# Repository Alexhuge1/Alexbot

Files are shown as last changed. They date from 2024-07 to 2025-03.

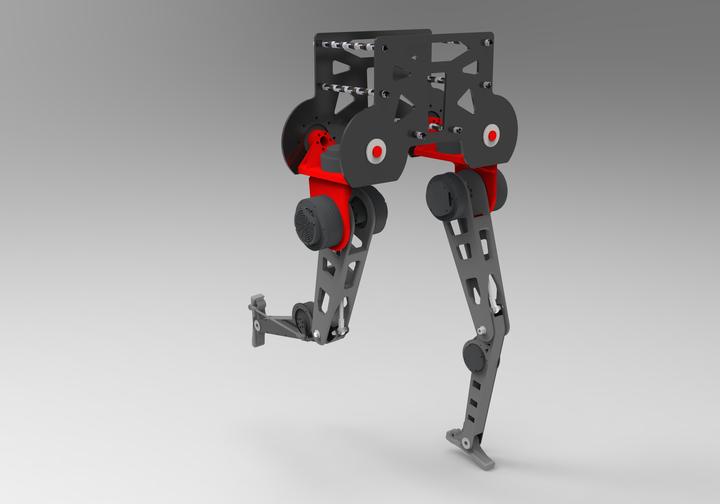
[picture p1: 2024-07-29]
Alexbot.jpeg

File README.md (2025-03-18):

latest version in https://github.com/Alexhuge1/Alexbotmini_hardware
建议直接使用第二代机器人，我们第三代在研发中，用的也是dm电机
## Language

- [English](#english)
- [中文](#中文)

---

### English

AlexBot is an open-source bipedal robots, designed with enhanced performance and a more rational structure. We have developed a complete set of open-source hardware for the robot, including the driving system, which allows it to walk dynamically. While it may not match the performance of commercial robots like the Unitree H1, our design is open-source and cost-effective.

<div style="text-align: center;">
    run
</div>

### Mechanical & Structure

Our robot features a leg with five joints: a 3-DOF hip joint, a 1-DOF knee joint, and a 1-DOF ankle joint. To reduce the overall inertia of the lower leg, we have moved the knee joint motor to the hip area. We use the Daimiao DM-J8009 for the hip joint of the thigh, with a rated torque of 20Nm and a peak torque of 40Nm. Other joints use DM-J8006, and the ankle joint uses DM-J6006. The mechanical design was done in SolidWorks 2021, with topological optimization and structural finite element simulation using Altair Inspire. The thigh parts are CNC machined, with an estimated cost of around 5000 RMB.

<div style="text-align: center;">
    Mechanical Design
</div>

### Hardware & Actuators

The hardware includes an STM32H7B0 core board with a 9-axis gyroscope for outer loop control. The upper computer uses an NVIDIA Jetson Xavier NX, and we are considering whether the TX2 could also be suitable. The entire circuit includes two power distribution boards, a control board with the STM32H7B0VBT6 as the core, and the Jetson Xavier NX as the upper computer. The power supply provides 24V to the motors, with a step-down module to provide 5V and 19V for the control board and Jetson Xavier NX, respectively.

<div style="text-align: center;">
    Hardware Overview
</div>

### Imitation Learning, Full-Body MPC, and WBC

Our gait planning is showing promising results, and the team responsible for the algorithms has successfully made the robot walk. We have adjusted the joint limits in the URDF file according to the electrical control specifications, which can be viewed using the MuJoCo viewer.

<div style="text-align: center;">
    Gait Planning
</div>

### Pricing

The total cost of the robot is estimated to be around 20,000 RMB. We have negotiated a price with Daimiao Motors, and they have agreed to provide the complete set of motors for 10,500 RMB, including a USB-to-CAN module and an H723 development board. The machining cost is estimated to be 6,000 RMB, and adding the Jetson and various bearings and standard parts, the total cost should be around 20,000 RMB.

### Documentation

Our open-source documentation includes中期文档和PPT, which are available for download. For more detailed technical information, please refer to our [Zhihu article](https://zhuanlan.zhihu.com/p/69235601413).

### Community

Our WeChat group has reached its maximum capacity, and we are now using an invitation-only system. Several individuals or teams have already successfully replicated our robot, BOM is updated.

---

### 中文

AlexBot是我们开源双足机器人的下一代产品，设计上注重提升性能和结构合理性。我们为机器人开发了一整套开源硬件，包括驱动系统，使其能够动态行走。虽然它的性能可能远远无法与Unitree H1等商业机器人相媲美，但我们的设计是开源且成本效益高的。

<div style="text-align: center;">
    运行图
</div>

#### 机械与结构

我们的机器人腿部设计有五个关节：3自由度的髋关节、1自由度的膝关节和1自由度的踝关节。为了降低小腿的整体惯量，我们将膝关节电机上移至髋部。我们使用达妙DM-J8009作为大腿的髋关节电机，额定扭矩为20Nm，峰值扭矩为40Nm。其他关节使用DM-J8006，踝关节使用DM-J6006。机械设计是在SolidWorks 2021中完成的，采用了拓扑优化和结构有限元仿真，使用的是Altair Inspire。大腿部分采用CNC加工，预计成本约为5000元人民币。

<div style="text-align: center;">
    机械设计图
</div>

#### 硬件与驱动器

硬件部分主要包括一个集成了九轴陀螺仪的STM32H7B0核心板，用于外环控制。上位机使用了英伟达的Jetson Xavier NX作为主电脑，我们也在考虑是否TX2也能够胜任。整个电路包括两个分电板、一个以STM32H7B0VBT6为核心的控制板和Jetson Xavier NX。电源为电机提供24V电压，并通过降压模块为控制板和Jetson Xavier NX提供5V和19V电压。

<div style="text-align: center;">
    硬件概览
</div>

#### 模仿学习算法、全身MPC和WBC

我们的步态规划已经取得了初步成果，负责算法的团队已经成功让机器人行走。我们根据电控的限位要求调整了URDF文件中的关节限制，可以通过MuJoCo查看器查看。

<div style="text-align: center;">
    步态规划
</div>

#### 价格部分

机器人的整体价格预计在20000元人民币左右。我们已经与达妙电机谈妥价格，他们同意以10500元人民币的价格提供整套电机，并附送USB转CAN模块和H723开发板。加工费用预计为6000元人民币，加上Jetson和各种轴承及标准件，总成本应该在20000元人民币左右。

我们的开源文档包括中期文档和PPT，可供下载。有关更详细的技术信息，请参阅我们的[知乎文章](https://zhuanlan.zhihu.com/p/69235601413)。

#### 社区

我们的微信群已满200人，现在采用邀请制度。已有数人成功复制了我们的机器人，BOM已更新。

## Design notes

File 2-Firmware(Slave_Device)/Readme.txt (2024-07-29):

How to use the code
leg02包含了USART01与上位机(Jetson)通讯、CAN1接左腿五电机级联、CAN2接右腿五电机级联、SPI通讯接受BMI088数据
包含了时钟，定时器等底层设计，同时进行了一些些简单的封装，方便基于函数开发，简单介绍一下程序架构：
1.在dm_driver.c中,其中电机使用MIT协议进行力控，使用void mit_ctrl(FDCAN_HandleTypeDef* hcan, uint16_t motor_id, float pos, float vel,float kp, float kd, float torq)来控制。
2.在Frame_function.c，写了上下位机通信的部分，包含了下位机的接收和发送，其中规定了帧的格式，如果传参变量发生修改请修改此函数。
3.在BMI088driver.c中，写了六轴加速度计的部分，包含了姿态解算得到姿态的欧拉角和加速度，同时还写了函数包含了使用四阶龙格库塔法来解算从欧拉角变到四元数。
----------------------------------------------------------------------------------------------
leg02 contains a USART01 and the host computer (Jetson) communication, CAN1 to the left leg of the five motor cascade, CAN2 to the right leg of the five motor cascade, SPI communication to accept BMI088 data.
Contains a clock, timer and other underlying design, while some of the simple package, to facilitate the development of function-based, simple introduction to the program structure:
1. in dm_driver.c, where the motor using the MIT protocol for force control, using void
 mit_ctrl(FDCAN_HandleTypeDef* hcan, uint16_t motor_id, float pos, float
 vel,float kp, float kd, float torq) to control.
2. In Frame_function.c, write the upper and lower computer communication part, including the lower computer to receive and send, which specifies the format of the frame, if the pass parameter variable is changed, please modify this function.
3. In BMI088driver.c, wrote the part of the six-axis accelerometer, which contains the attitude solving to get the Euler angle and acceleration of the attitude, and also wrote the function which contains the solving to change from Euler angle to quaternion by using the fourth-order Lunger Kuta method.

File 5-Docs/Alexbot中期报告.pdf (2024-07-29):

## 哈尔滨工业大学

## 大学生创新创业训练计划项目

## 中期检查报告

### 项 目 名 称：双足人形机器人 AlexBot

### 执 行 时 间： 2023 年 9 月至 2024 年 9 月

# 负 责 人：黄一 Alexhuge

### 学院及专业：未来技术学院

## 1、项目简介

现拟打算设计一套以伺服电机为驱动器的十自由度的双足机器人下肢 AlexBot，以研究双

足机器人运动规划与控制，首先对于机器人的结构以及控制系统进行设计以及拓扑优化；其 次，进行以髋部坐标系为基坐标系的正运动学及逆运动学分析，并计算了机器人的实时质心 位置以及机器人的质心相对于足端的雅可比矩阵；随后，说明了基于质心期望力的二维线性 倒立摆理论，分别对单足支撑阶段以及双足支撑阶段的支撑脚与摆动脚进行规划，再将二维 的情况推展到三维；之后，将线性倒立摆的行走数据当作参考在虚拟环境中对机器人进行强 化学习训练，其中包括神经网络的结构的设计，强化学习算法超参数的设置，奖励函数、训 练终止条件的设置以及将仿真迁移到现实机器人中需要进行的动态随机化策略；最后，为了 验证方法的可行性，分别在仿真以及现实中实验。

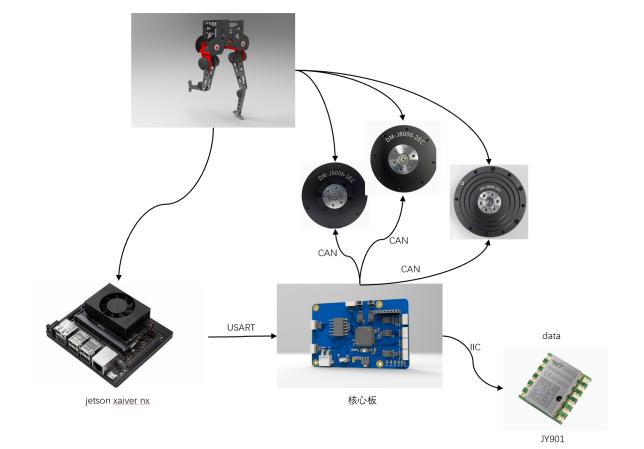
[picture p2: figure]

图 1-1 AlexBot 双足机器人设计仿真图 | 图 1-2 双足机器人架构图

## 2、立项背景

## 2.1 研究背景

在我国社会结构和经济发展的新阶段，人口老龄化问题已成为一个不容忽视的社会现象。 根据最新的统计数据，65 岁及以上的老年人口数量已经超过 1.8 亿，占总人口的比例达到 12.6%，并且这一比例预计将在未来持续增长。这一趋势的出现，对我国的劳动力市场产生了

显著影响。随着劳动力人口的减少，劳动力成本不断上升，这不仅对传统的经济发展模式提 出了新的挑战，也对现有的社会保障体系带来了前所未有的压力。 在应对人口老龄化的挑战中，机器人产业的发展显示出了巨大的潜力和重要性。通过引 入机器人技术，不仅可以有效缓解劳动力短缺的问题，还能显著提高生产效率和质量，从而 推动经济的持续健康发展。

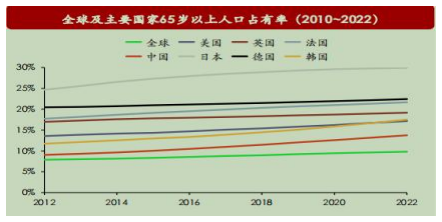
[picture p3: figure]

图 2-1 全球及主要国家 65 岁以上人口占有率

## 2.2 研究目的及意义

随着科技的不断进步，人们对机器人技术的需求和期待也在不断提高。在这一背景下， 足式机器人，尤其是双足机器人的研究和开发成为了机器人领域的热点之一。双足机器人相 较于其他类型的机器人，具有一系列独特的优势和潜力：它们不仅能够提高生产效率，保障 人员安全，还能够在服务领域发挥重要作用，推动人机交互和人机协同技术的发展。

图 2-2 人形机器人应用于人类日常生活

## 2.3 研究现状

从上个世纪中叶开始，双足机器人的研究逐渐成为全球科技领域的热点，研究者们从对 人类和各种动物的步行理论研究开始，随着科学技术领域的飞速发展，双足机器人的行走又 融合了运动控制、人工智能等方式，双足机器人的行走理论被逐渐完善。美国和日本在这一 领域的发展尤为突出，它们的研究成果不仅推动了机器人技术的进步，也引领了全球的研究 趋势。
美国波士顿动力公司的 Atlas 机器人和日本本田公司的 ASIMO 机器人就是近十年来在学 术界引起广泛关注的两大“网红”机器人。这些机器人不仅在技术上取得了飞速的发展，而且

在运动规划和稳定性控制方面也取得了显著的成就。半个世纪以来，这两个国家涌现出了许 多震惊学术界的先进机器人，如本田的 ASIMO 和波士顿动力的 Atlas，它们不仅在技术上达

到了新的高度，而且在实际应用中也展现出了巨大的潜力。

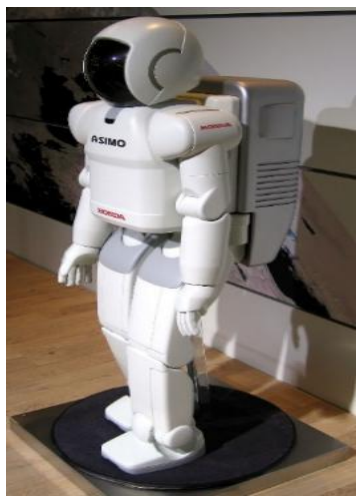
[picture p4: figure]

（a）ASIMO 机器人 | （b）ATLAS 机器人
图 2-3 美国和日本公司研发的部分人形机器人
特斯拉公司的人形机器人 Tesla Bot 在经历了多版本迭代之后，其研究进展远超预期。从

步态行走技术来看，Tesla Bot 从 2022 年完成第一次步态行走到 2023 年已经能够实现在工厂 内稳步行走；从功能来看，Tesla Bot 从第一版仅具备抓取、搬运、上下料功能到具备双手处 理复杂任务的能力，同时 Tesla Bot 关节电机转矩控制的精度已经可以达到在运动过程中不打 碎鸡蛋的水平。与此同时，Tesla Bot 与特斯拉车辆共享核心自研的感知技术（FSD Computer

## 和 DOJO Training），并且其搭载的 Autopilot Camera 所具备的强大的视觉处理能力使得 Tesla

Bot 在人形机器人研究领域处于领先地位。

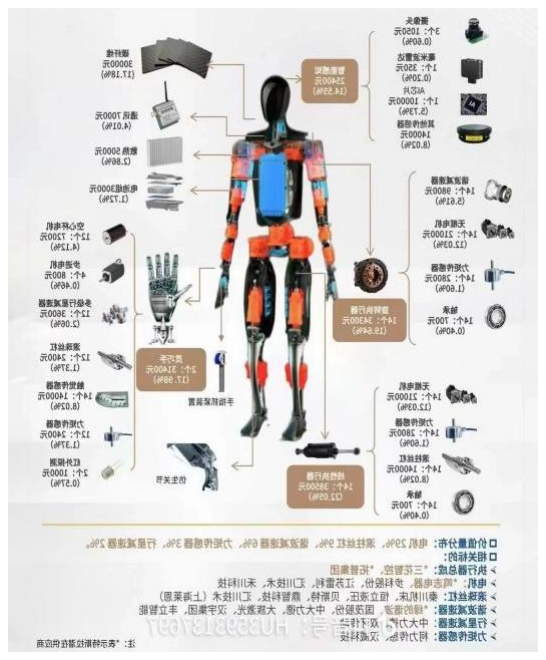
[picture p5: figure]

（a）特斯拉人形机器人 Optimus （b）Optimus 结构示意图

## 图 2-4 特斯拉公司研发的 Tesla Bot

中国在人形机器人产业的发展过程中，经历了从追赶到领先的转变，并逐步超越了早期 投入此领域的日本、美国和韩国。其中创业企业典型代表包括优必选科技、追觅科技、智元、 宇树、傅利叶智能等；科技企业典型代表则为小米、科大讯飞；高校领域则以哈尔滨工业大 学研制的 GoRoBoT 机器人、北京理工大学研制的 BHR 系列双足机器人、清华大学研制的

## Stepper-2D 机器人为代表。

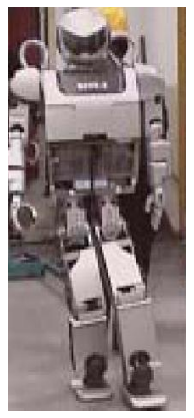
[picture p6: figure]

（a）宇树 H1 机器人（b）傅里叶 GR-1 机器人（c）BHR-2 机器人（d）优必选 Walker 机器人

图 2-5 国内部分双足人形机器人

## 2.4 研究趋势

随着人形机器人产业奇点将至，市场将会呈现出更加明显的马太效应。在未来很长一段 时间内，人形机器人的领域将围绕人类步态与行为的高度模仿、环境感知与交互能力的提升、 轻量化和能效优化等一系列方向进一步深化发展。未来随着技术的不断成熟和创新，人形机 器人尤其是双足机器人有望在更多领域展现其独特的价值和潜力。

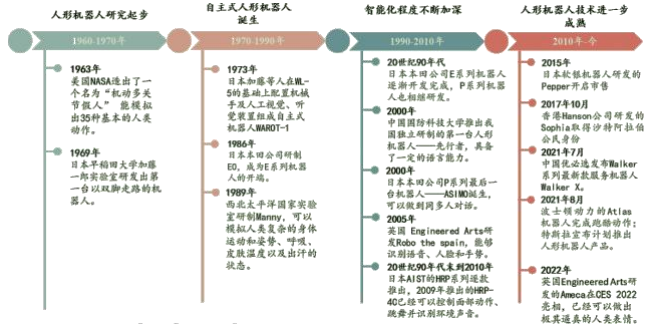
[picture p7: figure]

图 2-6 人形机器人发展历程及未来发展趋势

## 3、项目方案

本项目我们对双足机器人的行走进行研究，通过研究基于质心期望力的二维线性倒立摆 拓展到三维线性倒立摆，并通过强化学习算法得到神经网络控制器，使得双足机器人可以执 行行走任务，主要研究内容如下：
(1) 本项目想设计一套大型伺服双足机器人以供算法研究使用，同时严格控制成本并且编

写教程开源全结构、硬件、算法，提供一套双足的完整的解决方案，产生一定的影响力。
(2) 研究基于二维线性倒立摆的步态规划器，通过线性倒立摆的动力学性质进行规划，分

别对单足支撑期和双足支撑期进行规划，应用足底到质心的雅可比矩阵，将动力学简化模型 应用到复杂机器人上，通过反馈重新分配腿部力矩，使得双足机器人的能量足以越过势能高 点，形成稳态行走的步态，而后再将二维线性倒立摆拓展到三维线性倒立摆算法。
(3) 应用基于质心期望力的线性倒立摆所得到的规划步态形成参考轨迹，使用强化学习算

法，在虚拟环境中迭代训练，运用动态随机化策略，提高网络的适应度，以便将仿真中训练 的网络迁移到现实环境中。
(4) 将网络模型迁移到现实机器人身上，进行 Sim to Real 的行走实验，积累经验，提升机

器人的鲁棒性。

## 4、项目实施的进展情况及初步取得的成果

## 4.0 整体架构

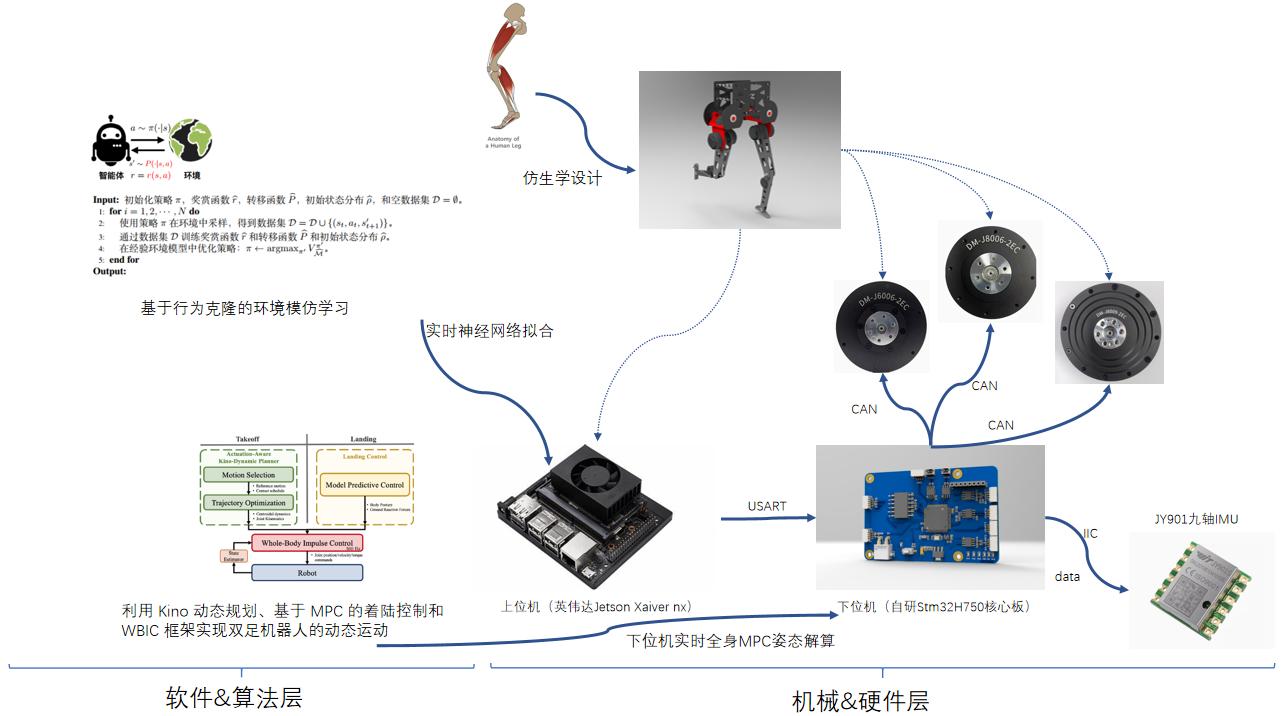
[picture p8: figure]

图 4-1 双足机器人架构图

本项目期望设计一套低成本，全开源，低入门门槛，完整系统的双足下肢机器人（之后 会设计上肢），方便形成双足开源生态，增加影响力和为更多工程师提供帮助。（类比 MIT 的 Cheetah 四足机器人）

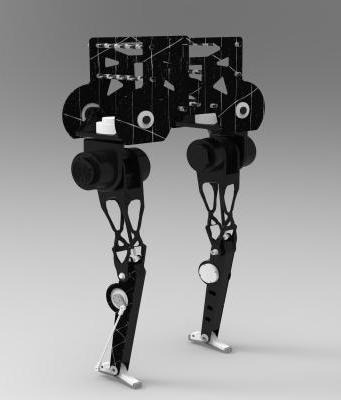
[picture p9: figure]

## 图 4-2(a) MIT Cheetah 四足机器人 图 4-2(b) HIT Alexbot 双足机器人

本项目涉及两套双足机器人结构，一套为研究三维线性倒立摆所需要的十自由度桌面级 机器人，其各个执行器都是在机器人矢状面内出力，配置以人类的下肢关节配置为参考，使 得机器人得以在三维平面内行走。另一套为大型研究步态以及迭代优化双足架构的大型双足 机器人。

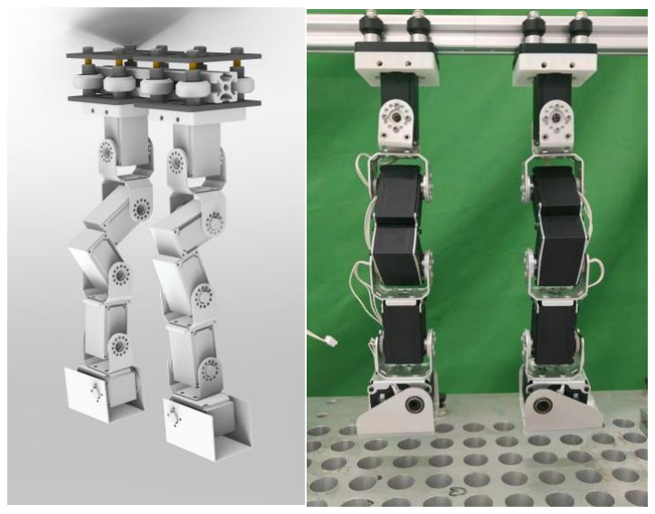
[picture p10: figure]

图 4-3(a) 研究性桌面级双足机器人 | 图 4-3(b) AlexBot 双足机器人下肢

我们先对两套双足机器人结构进行设计，搭建控制系统，此外为后续进行步态规划打下 基础，对两套机器人分别进行正运动以及逆运动学分析，使得给定足端位姿可以求解各关节 角度，给定各关节角度可以求解足端位姿。同时，通过给定关节角度以及髋部位姿，得出机 器人实时的质心位置，求解足端到机器人质心的雅可比矩阵。

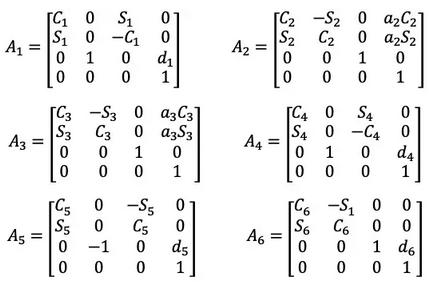
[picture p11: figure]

图 4-4(a) D-H 法正解双足姿态 | 图 4-4(b) D-H 法逆解双足姿态

同时应用对于机器人的运动学计算结合线性倒立摆算法对支撑腿、摆动腿以及双足支撑 阶段进行规划和控制，同时在仿真物理环境 Mujoco 中进行稳定行走，生成二进制数据，通过 agent 与环境的自主迭代互动，向着累计回报最高的方向进化，为了提高效率，同时为了避免

强化学习学习的步态与人类行走步态相差过大，采用基于参考轨迹的强化学习方法，我们利 用近端策略优化的强化学习算法训练神经网络控制器，在基于质心期望力的线性倒立摆的运 动规划器所形成的参考轨迹的基础上进行学习训练，对于算法的流程、状态及动作空间以及 奖励函数进行了设计，引入了动态随机化策略使得网络更容易迁移到现实机器人之中，进行 强化学习步行控制器的设计。

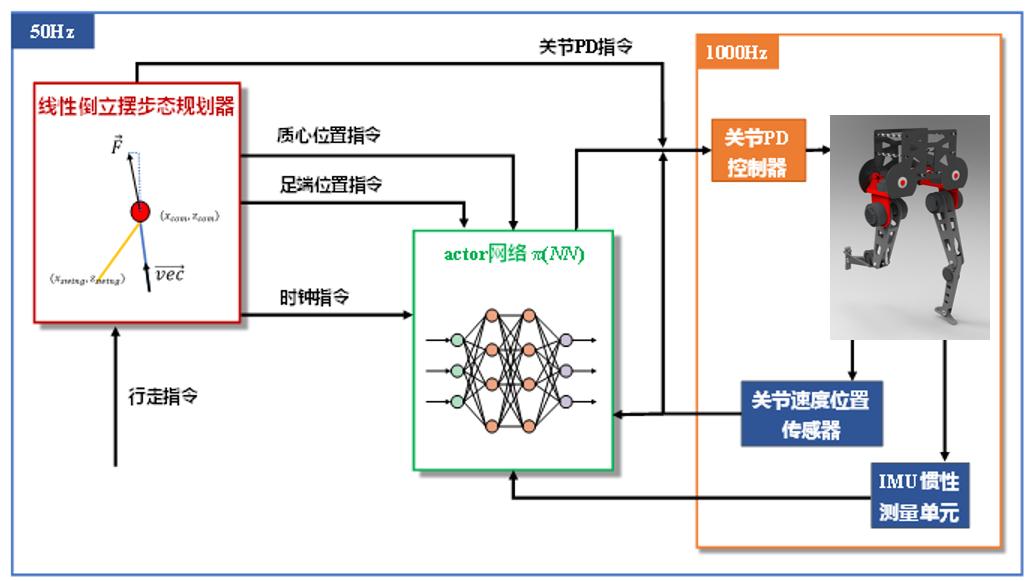
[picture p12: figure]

图 4-5 AlexBot 双足机器人基于倒立摆规划器的神经网络框图

为了验证强化学习的可行性，将从仿真和实物两个层面来进行算法验证。首先在仿真实 验中分别进行机器人的行走实验，由于发现通过强化学习所得到的网络具有一定的鲁棒性， 故额外进行了抗干扰力实验，并进行抗干扰训练提升机器人的抗干扰能力。同时将进行最为 困难的 Sim To Real 迁移实验，实现双足机器人的行走和实现更多动作。

## 4.1 机械部分

4.1.0 机械总论

本项目目标是研制一款双足机器人，具有轻量化的结构以及优秀的性能和合理分配的惯 量以及合适的运动性能。基于轻量化的考虑，本项目首先分析人体腿部结构以及肌肉分布和 腿部惯量，使用一体闭环私服关节电机以及有限元分析 Altair Inspire 分别代表人体的肌肉以

及骨骼，使用最小体积质量比目标对机械腿的框架结构进行优化设计，并将拓扑优化结果导 入到 SolidWorks 软件中，在考虑加工条件的前提下对零件进行修形，得到了满足强度要求且 轻量化的机械腿的结构件。同时，机器人使用轻量化的结构件加工而成，如 3K 碳管，3K 碳 纤维板，铝 6061 等材料，既兼顾材料重量也兼顾材料强度。
AlexBot 双足机器人包含单腿 5 自由度，其中包含三个髋关节自由度、一个膝关节自由度、

一个踝关节自由度。其中为了整体惯量考虑，我们整体上移膝关节自由度并使用板簧结构传 动到膝盖部分，对于踝关节自由度亦如此。通过惯量的计算以及参数测量，我们最终选定三 款一体闭环驱动电机，分别为 DM-J8009、DM-J6006、DM-J8006。具有双编码器，输出轴单

圈绝对位置，不惧掉电输出轴绝对位置丢失。同时电机和驱动器一体化设计，结构紧凑，集 成度高。支持上位机可视化调试，支持固件升级。可通过 CAN 总线反馈电机速度、位置、

转矩、电机温度等信息。位置模式下支持梯形加减速。对于安全方面，具有双温度保护功能， 保证电机稳定运行。

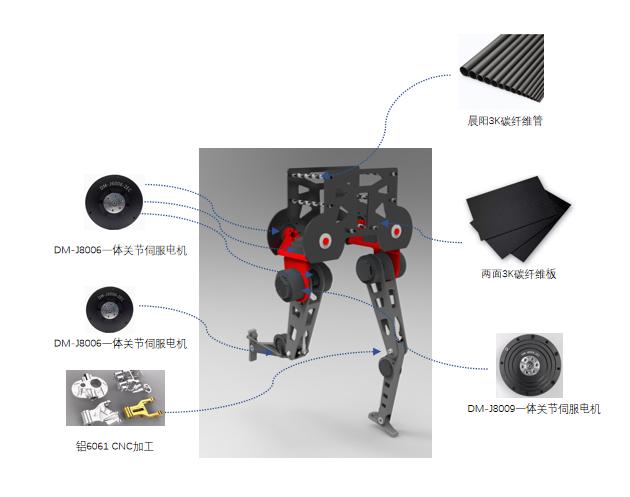
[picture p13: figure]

图 4-6 AlexBot 双足机器人机械结构以及关节自由度分配与限制角度

4.1.1 设计需求分析——腿部结构设计分析

在植物和生物的世界里，生物系统的基本结构往往是向着最优能源消耗的方向进化的， 相比较于现有的机械结构而言，生物结构的重量更轻、寿命更长，并且具有一定的柔性。自 然界生物进化的一个特点是“用进废退”，在需要承受较大载荷的地方会优先进化，在承受较

小载荷的地方，则会发生退化。如长颈鹿的祖先的脖子并没有现在这么长，但是由于气候问 题，较矮的灌木不复存在，为了吃到更高的乔木上的枝叶，长颈鹿的脖子渐渐往长的方向进 化。人类作为灵长类动物，双足步行已有数百万年的历史，因此在机械腿设计中，可以参照 人体运动学和构造来设计机械腿。
人体的腿部结构主要存在 6 个自由度，分别是髋关节的屈伸/伸展（俯仰、pitch）、内旋/ 外旋（偏航、yaw）、外摆/内收（翻滚、roll）三个自由度，膝关节的屈伸/伸展自由度，踝关 节的屈伸/伸展、外摆/内收两个自由度。在本文的设计的柔顺机械腿中，主要研究的自由度为 髋关节和膝关节的屈伸/伸展自由度，这是因为这两个自由度在人体运动中承受了最大的载荷，

直接为人在行走、跳跃、奔跑等过程中重心的位移提供动力。 人体腿部整体外形曲线呈上粗下细的倒三角，如图 4-7 所示，这是因为人在运动过程中腿

部存在支撑相和摆动相这两个状态，倒三角的结构有利于减小腿的转动惯量，提高腿在摆动 相过程中的动态性能。在机械腿设计中，应该参照人体腿部结构，设计符合人体动力学的“上 重下轻”的机械腿。此外，应该尽可能减少机械腿结构的重量，小腿的质量要小于大腿，机械

腿结构重量的降低使得机械腿可以选择更小、更轻的驱动器，减少机械腿质量的同时可以调 高其动力学性能。人体膝关节处有复杂的半月板-韧带结构，如图 4-7 所示，其中，半月板负

责行走、跳跃、奔跑等过程中对外部冲击的缓冲以及膝关节运动的润滑，韧带负责连接肌肉 与骨骼，提供动力。做过半月板切除手术的运动员膝盖往往容易再次受伤，其原因就是在切 除了半月板之后，运动员股骨和胫骨连接初缺少缓冲和润滑，在进行跑跳等动作时膝盖会受

关节 | 自由度 | 角度 (rad)

髋关节

| 横滚 | -0.345~1.222
| 俯仰 | -1.222~1.222
髋关节 | 横滚 | -1.047~1.047
膝关节 | 俯仰 | 0~1.571
踝关节 | 俯仰 | -1.047~1.047

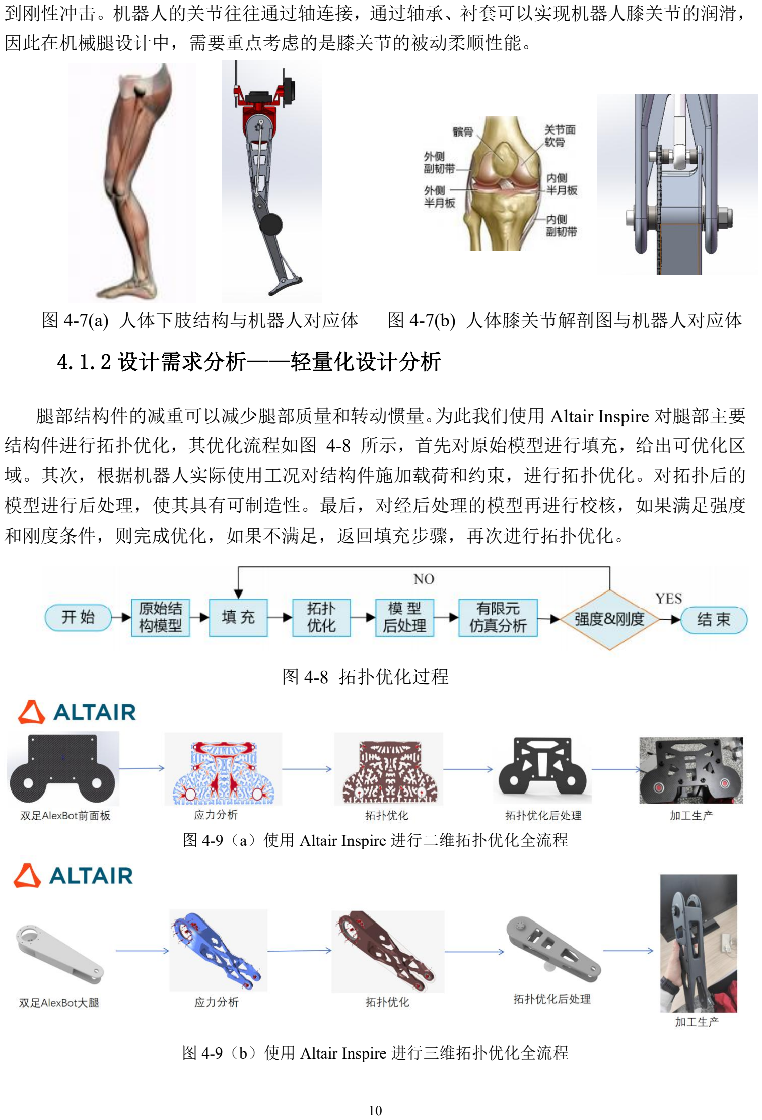
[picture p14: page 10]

到刚性冲击。机器人的关节往往通过轴连接，通过轴承、衬套可以实现机器人膝关节的润滑， 因此在机械腿设计中，需要重点考虑的是膝关节的被动柔顺性能。

图 4-7(a) 人体下肢结构与机器人对应体 图 4-7(b) 人体膝关节解剖图与机器人对应体

4.1.2 设计需求分析——轻量化设计分析

腿部结构件的减重可以减少腿部质量和转动惯量。为此我们使用 Altair Inspire 对腿部主要 结构件进行拓扑优化，其优化流程如图 4-8 所示，首先对原始模型进行填充，给出可优化区

域。其次，根据机器人实际使用工况对结构件施加载荷和约束，进行拓扑优化。对拓扑后的 模型进行后处理，使其具有可制造性。最后，对经后处理的模型再进行校核，如果满足强度 和刚度条件，则完成优化，如果不满足，返回填充步骤，再次进行拓扑优化。

图 4-8 拓扑优化过程

图 4-9（a）使用 Altair Inspire 进行二维拓扑优化全流程

图 4-9（b）使用 Altair Inspire 进行三维拓扑优化全流程

以双足前面板为例，AlexBot 采用前后双碳板通过碳管固定，通过在 Altair Inspire 添加载荷与 固定点实现最小化质量与最大应力比进行 2 维拓扑优化，如图 4-9（a）所示。3 维拓扑优化

同理。

4.1.3 运动周期分析

在机器人行走过程中，可以将一只脚着地到下一次着地这一段时间划分为一个运动周期。 在本文的设计中，不考虑脚掌的设计，仅仅将其看成一个支点，因此可以将行走步态下机械 腿的运动周期划分支撑相和摆动相两个状态。在行走过程中，机械腿需要为整个机器人质心 的运动提供能量支持，在摆动腿落地瞬间，摆动腿切换为支撑腿，依靠机器人自身行走的惯 性和膝关节的伸展 将质心从谷点推动到峰点，随后利用重力和膝关节的弯曲将质心从峰点降 回至谷点，完成支撑相周期，期间髋关节的屈伸/伸展自由度需要配合膝关节的角度实时调整

上半身的质心位置，防止机器人出现倾翻的状况；机器人双腿在摆动相和支撑相中相互切换， 当其中一只腿处于支撑相时另一只腿则处于摆动相，准备下一次与地面接触。具体的步行中 状态变化图如图 4-8 所示。从图中可以看出机器人在运动过程中，机械腿在摆动相和支撑相

的切换瞬间，该腿与地面发生冲击，机器人垂直方向的能量瞬间被释放，在膝关节处的缓冲 就显得尤为重要。虽然本文的线性/弹簧倒立摆步态已经考虑了落地时的冲击，但是在实际工

作过程中，由于控制器与作动器的延迟，冲击依然存在，因此机械腿设计时需要考虑其被动 柔顺性。此外，根据倒立摆模型的建模特性（机器人被看作质心和无重量的腿），在设计时， 机械腿的重量需要尽可能轻，以保证机械腿的动态性能。从运动周期可以看出，机器人机械 腿设计需要重点考虑柔顺性和轻量化，这也与前文的分析不谋而合。我们使用斯坦福大学的 软件 OpenSim 实现人形结构的奔跑对应的肌肉与骨骼运动分析。

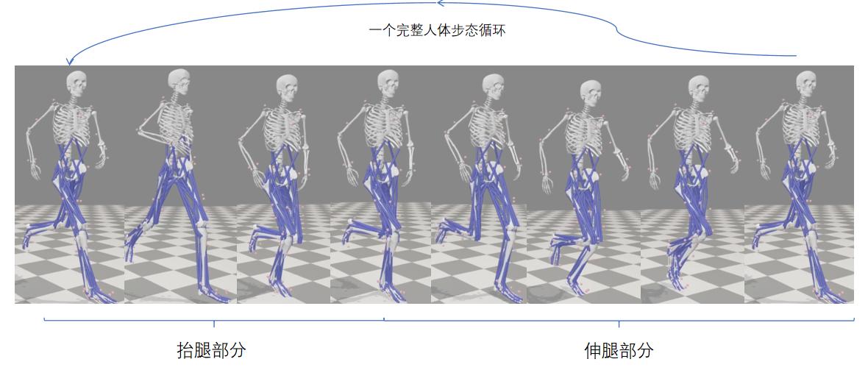
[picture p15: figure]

图 4-8 OpenSim 仿真人体一个完整的跑步姿态

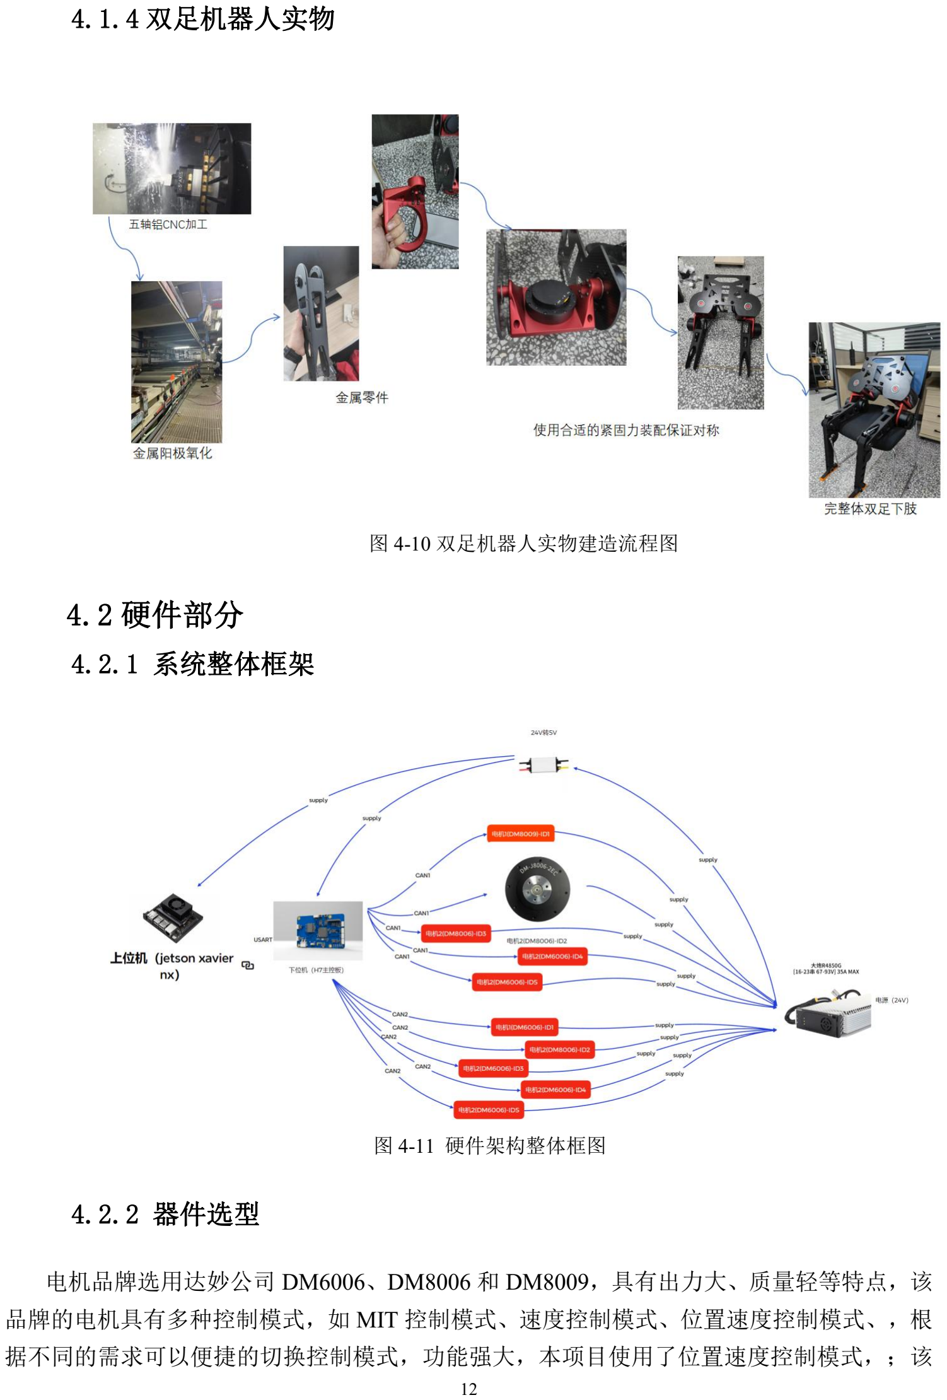
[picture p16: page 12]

4.1.4 双足机器人实物

图 4-10 双足机器人实物建造流程图

## 4.2 硬件部分

4.2.1 系统整体框架

图 4-11 硬件架构整体框图

4.2.2 器件选型

电机品牌选用达妙公司 DM6006、DM8006 和 DM8009，具有出力大、质量轻等特点，该 品牌的电机具有多种控制模式，如 MIT 控制模式、速度控制模式、位置速度控制模式、，根

据不同的需求可以便捷的切换控制模式，功能强大，本项目使用了位置速度控制模式，；该

品牌电机都配备了绝对值编码器，同时响应速度快，满足整个系统对于快速性的要求。 其中三种电机 DM6006 的额定电压为 24V 但支持 48V 输入，额定电流为 4A，额定的扭 矩为 4NM。DM8006 电机的额定电压为 24V 可支持 48V 输入，额定电流为 6.5A，额定的扭 矩为 8NM。DM8009 电机额定电压为 48V，可支持 24V 输入，额定电流为 20A.。考虑到整个 功率以及供电的需求，我们这里统一采用 24V 对三种电机供电，根据不同关节所需的扭矩的

不同，我们分别选取不同的电机。

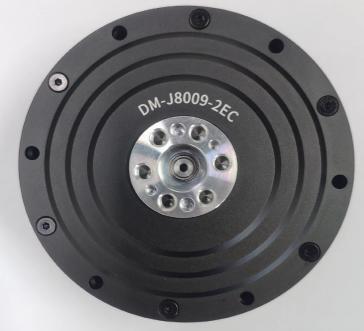
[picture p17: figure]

图 4-12(a) DM-J6006 | 图 4-12(b) DM-J8006 | 图 4-12(c) DM-J8009

IMU 惯性测量单元选用维特智能公司的 WT-901C 型号，其具有精度高，速度快，误差小 等优点，具有六轴和九轴的算法，可以根据需求选取模式，加速度计分辨率为 0.0005

## g/LSB,RMS 噪声在 0.75 到 1 mg-LSB 之间；陀螺仪分辨率为,RMS 噪声在 0.0028 到之间；俯

仰角及横滚角的分辨率为 0.0055°，其倾角精度为 0.2°，可以满足双足机器人使用的反馈精

度。
在电源选取上，我们一共所需四个 DM6006 电机，四个 8006 电机以及两个 DM8009 电机， 根据他们的额定电压和额定电流，这里我们假设他们的输入电压都为 24V，我们可得到总的 功率为 1968W 的功率。所以我们这里选取了输出功率为 2KW 的 DC 直流源作为我们的供电

电源。

图 4-13(a) JY901 九轴传感器 | 图 4-13(b) DC 直流源

4.2.3 硬件设计

整体电路所包含的电路板总共如下，包含两个分电板以及一个 STM32H7B0VBT6 为核心

## 的控制板和上位机 jetson Xavier nx。由电源供电 24V 给到 4 个 DM6006，4 个 DM8006 和两 个 DM8009。接入 24V 转压模块输出 5V 和 19V 电压分别给主控核心板和 jetson Xavier nx 供

电，主控核心板主要处理矩阵变换以及和电机之间的 CAN 通讯问题，一条腿一共有五个电机，

分别是两个 DM6006,DM8006 和一个 DM8009,考虑到 CAN 总线带宽的占用问题，一个 STM32H7B0 核心板的一个 CAN 通道最多接入 5 个电机，也就是一条腿的所有电机。CAN1 接入左腿的五个电机，CAN2 接入右腿的两个电机。同时核心板皆有带有隔离的多路串口和

## RS485 接口。可以顺利的完成和 jetson Xavier nx 的通讯。

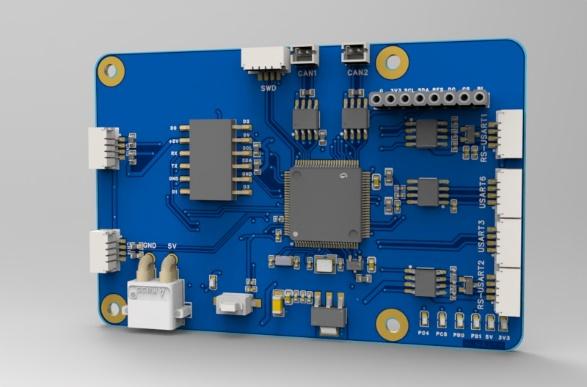
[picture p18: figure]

（a） 中心板 1 | （b） 核心板渲染图

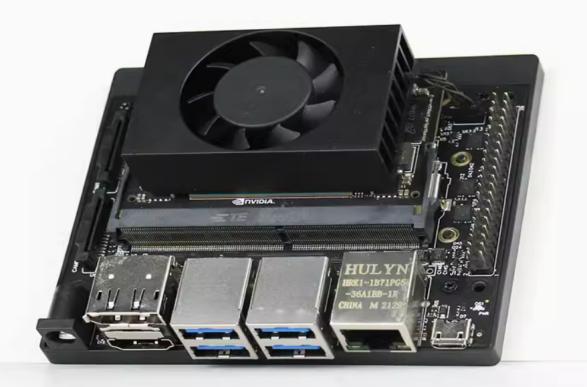
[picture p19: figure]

（c） 中心板 2 | （d） jetson Xavier nx
图 4-13 硬件部分板子

## 选用 STM32H7B0VBT6 作为核心芯片，引出两路 CAN 通道 FDCAN1 和 FDCAN2。电路

设计包含输入的 5V 过压保护设计，通过一个 PNP 和一个 P-MOS 来完成电路过压时自动断开 电路并直接接入 GND。同时内置 IMU，可以选择多种方式与之通讯，可以通过模拟 IIC 来获 取九轴数据或者通过串口实现九轴的数据获取。同时板内内置两路 485 通讯接口，通过 MAX13487RS485 逻辑电平转换芯片，将 TTL 电平转换成 RS485 协议的电平，并通过外部电

路的设计实现数据传输的自动换向，同时引出多路串口接口，为了防止高压通过串口直接损 坏芯片，在每一路的串口输出中，接入了Π122M31 隔离芯片进行隔离。并引出几路定时器接 口可以输出 PWM 波方便后续方案改进或者调试。

图 4-14（a） 核心板原理图 | 图 4-14（b） 核心板 PCB 图

## 4.3 驱动部分

一条腿上一共有五个自由度，一个 DM8009 电机，两个 8006 电机和两个 6006 电机。

## DM8009， DM8006 和 DM6006 电机是 24V 供电。考虑到实际功率的需求，这里选用 XT60

作为我们电源的输入接口，其中 XT30 作为 24V 供电的接口。从模型上侧接入，一个 XT60 接入 24V 电源，并通过同板的另外两个 XT60 接入两个 DM8009,同时最后一个 XT60 接口接 入另一个电源中心板，好给 DM8006 和 DM6006 电机进行供电。

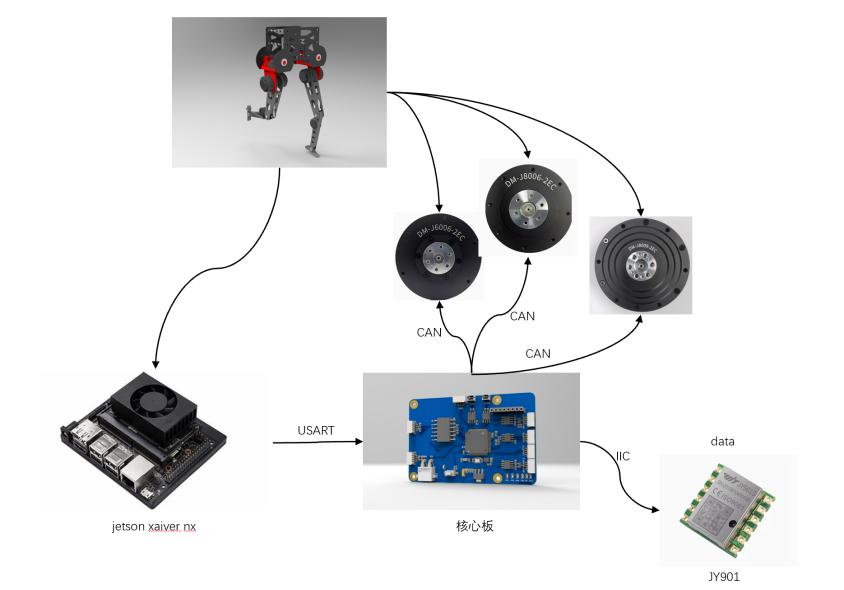
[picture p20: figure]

图 4-15 控制框图
代码编写我们选用 CUBEMX 软件进行配置编写，以下为代码的引脚配置情况整个引脚 FDCAN1 接入左腿的五个电机，FDCAN2 接入右腿的五个电机。DM 电机控制采用 CAN 通 讯协议，这里我们通过对 DM 电机发送 CAN 指令来实现对电机的控制。以下为电机速度控 制的协议：每次发送 8bit 的数据，要传输的速度数据为 float32 位类型，所以我们这里选择发 送 4 次来完成一个速度指令的传输。加速度计的通讯方式有很多，有串口和 IIC，这里我们选 用软件 IIC 获取九轴数据。以下为我们实际九轴数据获取的代码，如图 4-19 所示。关节控制 就是对多个电机进行控制，这里我们先通过 DM 的上位机对各个关节的电机的 ID 进行修改 好，我们对总的代码进行各个电机的控制，如图 4-20 所示。具体控制代码和效果如下：

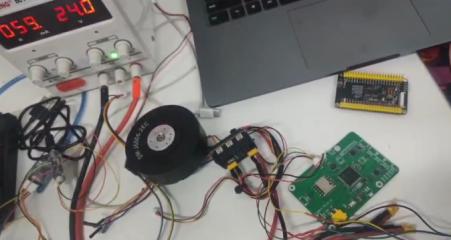
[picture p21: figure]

图 4-16 速度环控制 | 图 4-17（a） 速度控制 CAN 协议代码与引脚配置

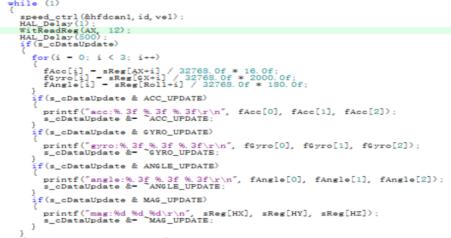
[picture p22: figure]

图 4-17(b) 九轴加速度计代码 | 图 4-17(c) 关节控制代码

## 4.3 算法部分

4.3.1 PPO 算法背景

让机器人像人类一样学习和做出人类的动作，一直是人工智能不断发展和完善的不竭动 力和目标，深度学习和强化学习的不断进步和发展极大地促进这一目标的实现。 深度学习的 发展把从原始的数据中提取高水平特征变成现实。深度学习在感知能力表现强势，但是在决 策能力上不尽人意;与此相反，强化学习在决策能力上表现上佳，但是对感知问题无特别优势。

因此，将两者结合起来优势互补，为解决复杂系统的感知决策问题提供了方法。将具有感知

## 能力的深度学习(deeplearning，简称 DL）和具有决策能力的强化学习 (reinforcement learning， 简称 RL）优势互补的结合在一起，构成深度强化学习(deep reinforcement learning,简称 DRL)

算法。人类的进化是不停地通过学习的方式获得经验知识，这也是人类不同于其他生物的重 要特点。因此在人工智能领域该如何教导机器人或者智能体学习人类的动作或者拥有人类的 学习方式是一个十分重要的研究课题。机器学习是一门复杂而涉及众多学科的门类，强化学 习(Reinforce Leaming，简称 RL）理论与算法和学习心理学与动态规划等至关重要。

策略梯度是一种常用的策略优化方法，它通过不断计算策略期望总奖赏关于策略参数的 梯度来更新策略参数，最终收敛于最优策略．因此在解决深度强化学习问题时，可以采用参 数为θ的深度神经网络来 进行参数化表示策略，并利用策略梯度方法来优化策略．值得注意 的是，在求解深度强化学习问题时，往往第一选择是采取基于策略梯度的算法．原因是它能 够直接优化策略的期望总奖赏，并以端对端的方式直接在策略空间中搜索最优策略，省去了 繁琐的中间环节．因此与 DQN 及其改进模型相比，基于策略梯度的 DRL 方法适用范围更广，

策略优化的效果也更好。

## PPO(Proximal Policy Optimization Algorithms)是目前应用最广的强化学习算法，在对传统

策略梯度算法引入使用 KL 散度决定参数，深度神经网络和 clip object 等方法之后，解决了在 线强化学习(on-policy)容易更新过大，容易过冲的问题，且收敛快，效果好，被作为强化学习 的范式使用。目前许多使用深度强化学习的机器人控制方案都是基于 PPO 算法的改进。

4.3.2 模仿学习

模仿学习（Imitation Learning）——从专家示例中学习——是一种让智能体（机器人）像

人类专家一样能够进行智能决策的方法。在通往通用人工智能的路上，人们发现很难手工地 进行编程来教会智能体进行思考，因为这么做涉及到大量的人工工程。比如，在教会车辆自 动驾驶的过程中，需要有大量的约束进行考虑（安全驾驶而不发生事故、平稳驾驶而增加舒 适感）等等，而针对这些约束设计特定的监督信息信号来引导智能体是一个比较困难的任务。 相反之下，人类却能比较容易地完成这些任务，并且为智能体提供大量的示例行为。利用这 些专家示例来教会智能体进行智能决策就是模仿学习主要解决的问题。通用地来讲，任何希 望智能体能够像“专家”一样进行决策的系统都能从模仿学习的方法里受益。事实上，在 20

## 世纪 80 年代末，卡内基梅隆大学（Carnegie Mellon University）的 Pomerleau 教授已经利用

人类专家示例成功地训练一个浅层神经网络，使得其控制的无人车能够穿越北美洲。前几年 大放异彩的 AlphaGo，第一个打败人类顶尖选手的机器人，也用到了模仿学习方法对人类棋

谱进行学习。除此之外，在现代的应用中，比如推荐系统，互联网网约车派单等系统中，也 用到了模仿学习的方法来构建一个虚拟世界，从而允许智能体在其中自由地试错和学习。不 断涌现的新的任务促使研究者们设计了各种各样的模仿学习算法。其中，普遍认为模仿学习

## 有两大类算法：行为克隆（Behavioral Cloning）和对抗式模仿学习（Adversarial Imitation

Learning）。其中，行为克隆算法尝试最小化智能体策略和专家策略的动作差异，把模仿学习

任务归约到常见的回归或者分类任务。而对抗式模仿学习算法则是通过逆强化学习 （InverseReinforcementLearning）来构建一个对抗的奖赏函数，然后最大化这个奖赏函数去模

仿专家行为。基于这两种基本的算法设计思路，研究者们提出了各种各样的模仿学习算法变 体。
机器人是模仿学习主要的研究领域，要解决如何让机器人像人一样行走，方式之一就是 使用人类行走的数据集对智能体进行训练。我们适配的 Loco-mujoco 项目提供了大量人类行

走的数据集，且规范了统一接口。

4.3.3 实施方案

本项目主要使用 PPO Agent 作为主要的强化学习方法，在基础的 PPO 算法上增加经验回 放，使用 pytorch 库中的 torchrl 搭建而成。在 isaac gym 平台上，通过使用 api 创造不同材质 和起伏的地面，使双足机器人具有适应各种地面的能力。适用于 Mujoco 的强化学习框架已经

## 搭建并测试完成，并成功应用于 Loco-mujoco 的 benchmark 环境。

经验回放（Experience Replay）是在线强化学习中的一个技术，旨在改善学习的效率和稳

定性。在实时与环境交互中获得的经验（状态、动作、奖励等）通常会被立即用于更新模型， 但是实时更新的模型常常由于较少的数据二变得不稳定，经验回放通过存储这些经验到一个 称为“经验回放缓冲区”的数据结构中，然后在训练过程中随机抽样以用于模型更新，从而 解决了这一问题。
仿真环境的搭建是双足机器人强化学习中的重要一步，本项目先后使用 isaac gym 和 mujoco 作为训练的仿真环境，isaac gym 是英伟达开发的支持 Gpu 运行的并行化仿真环境， 以解决强化学习普遍存在的仿真数据获取较慢的问题。Mujoco 是一个强大的物理引擎，对软 物体，肌腱，生物肌肉等结构也有仿真能力，使用 Mujoco 平台极大提高了本项目的拓展性，

可以在强化学习的基础上应用模仿学习。

## 5、特色与创新

5.1 极低的成本实现较强的运动性能

本双足机器人采用较易获取的材料和简易的 CNC 加工方式，争取将双足成本做到两万以

## 内，使用达妙 DM-J8006*6;DM-J8009*2;DM-J6006*2，额定扭矩分别为 8NM;20NM;4NM，通

过轻量化设计与降低腿部惯量实现。

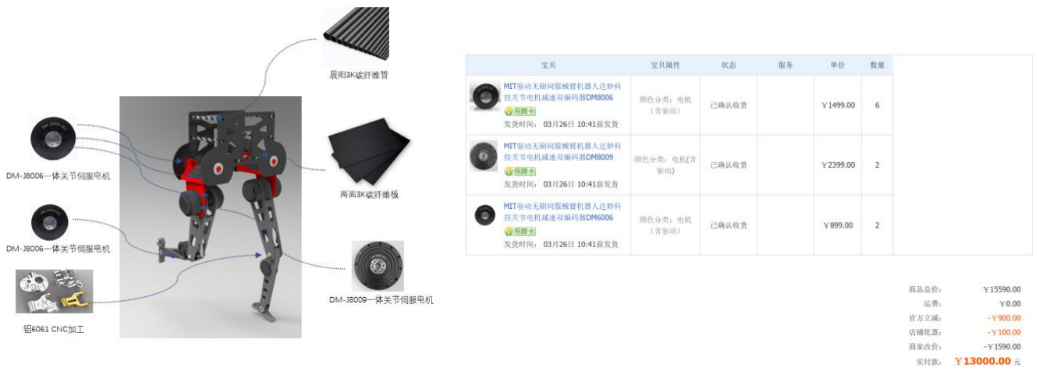
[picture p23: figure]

图 5-1 AlexBot 双足机器人机械结构以及部分订单价格

5.2 开源属性增加社群影响力

本双足机器人计划全部开源，包含机械结构设计，硬件设计，控制算法。目前开源机

械结构设计，硬件设计，目前产生一定影响力，有部分社会人士愿意资助此项目落地，

同时社群目前已有机器人相关硕博十余人密切关注，交流指导。
5.3 腿部关节以及计划足式仿生学设计

我们拟打算在结构设计上对于足踝关节进行仿生学设计。足踝关节是连接人类足部与

腿部的生物机械结构，在人类行走中扮演着至关重要的角色。其主要功能包括负重、提

供弹性以减轻地面冲击，并具备柔性以适应不平坦的地面。足踝关节由多个解剖结构组

成，包括胫骨的下端关节面、内踝关节面、腓骨的外踝关节面，以及距骨滑车的上关节

面和内外关节面。内踝和外踝是足踝关节的两个重要部分。在冠状面内，外踝相对于内

踝较低，大约低 1 厘米左右；在矢状面内，外踝相对于内踝稍微向后倾斜 1 厘米；后踝

相对于前踝向下延伸，从而限制了距骨向后移动。在正常的人类步态周期中，足踝关节

发挥着重要作用。在触地前期，当胫骨绕足踝关节旋转时，跟腱被拉长，并储存能量。

在触地后期，足踝关节向下蹬地，释放触地前期储存的能量。在摆动前期，足踝的跖屈

肌协助加速胫骨向前运动，为摆动腿提供主要动力。足踝关节的正常运动范围通常为背

伸 26°至 27°和跖屈 40°至 45°。

目前，双足机器人一般采用不同类型的足部结构，包括平足、弧形足和球状足，以实

现步行和稳定性。举例如 ASIMO 系列双足机器人、McGeer 被动步行机、康奈尔完全被

动机器人以及 RABBIT 平面双足机器人等。然而，与人类的高效、快速和稳定行走相比，

现有的双足机器人在运动性能方面仍有改进的空间。为了提高机器人在不平坦地面上的

行走稳定性并实现更自然的步态，研究人员致力于通过模仿人类足踝的功能来设计新型

的仿生足踝结构。通常情况下，双足机器人的踝关节是刚性的结构，而人类的足踝具有

刚柔耦合的结构。在人类行走时，内侧纵向足弓的弯曲和扭曲所产生的桁架机制和绞盘

机制使足趾能够吸收地面冲击并执行蹬地行为。这种刚柔耦合的结构使得人类足踝在行

走时能够适应不同地形和吸收地面的不平坦性，从而提供了更好的行走稳定性。因此，

将类似的机制引入双足机器人的足踝结构，可以帮助提高机器人的运动性能，使其更有

效地应对复杂的环境和地形。

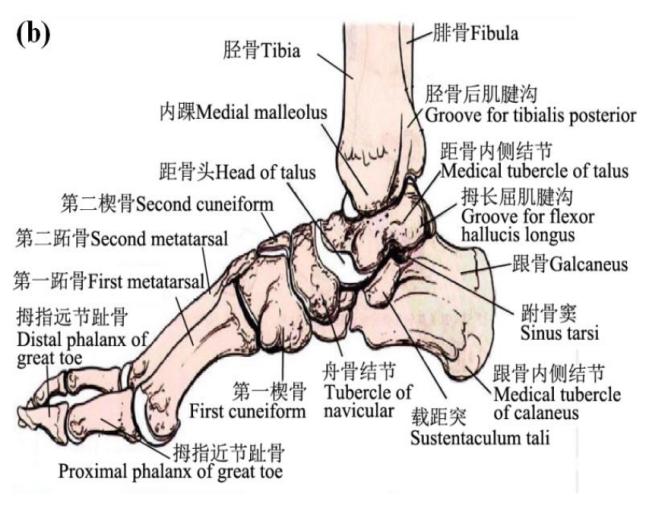
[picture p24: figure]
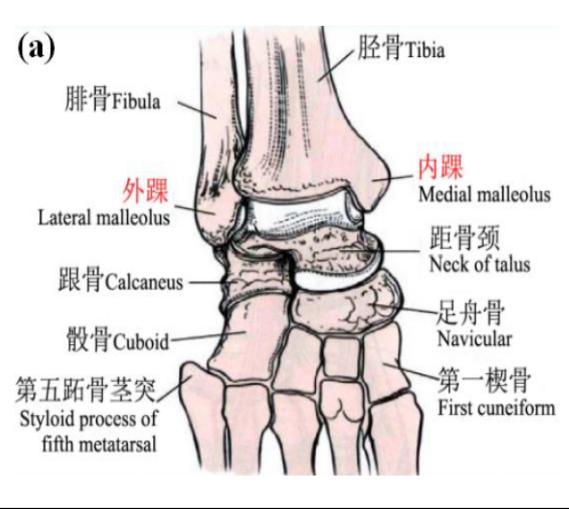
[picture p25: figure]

图 5-2 足踝骨骼组成（a）踝关节冠状面 | 图 5-2 足踝骨骼组成（b）踝关节矢状面

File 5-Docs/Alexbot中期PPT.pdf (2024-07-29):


组长：黄一 组员：赵之也 任飞 朱骐 张堡鑫
指导老师： 朱延河教授

# 双足人形机器人 结构与步态规划

目录
项目背景 | Catalogue


B A C K G R O U N D

01

### 项目方案

P r o j e c t P L A N

02

### 项目实施进展

P r o j e c t P r o g r e s s

03

### 项目特色与创新

P r o j e c t f e a t u r e s a n d i n n o v a t i o n

04

### 项目收获 05

P r o j e c t g a i n s


01

# 项目背景

B A C K G R O U N D


人口老龄化问题日益严重：根据最新的统计数据，
65岁及以上的老年人口数量已经超过1.8亿，占总人
口的比例达到12.6%。随着劳动力人口的减少，劳
动力成本不断上升，这不仅对传统的经济发展模式
提出了新的挑战，也对现有的社会保障体系带来了
前所未有的压力。
人形机器人具有独特的优势和潜力：双足机器人
相较于其他类型的机器人，不仅能够提高生产效率，
保障人员安全，还能够在服务领域发挥重要作用，
推动人机交互和人机协同技术的发展。


4

简介 BRIEF INTRODUCTION


国外研究现状：美国波士顿动力公司的Atlas机
器人和日本本田公司的ASIMO机器人就是近十年来
在学术界引起广泛关注的两大“网红”机器人。这
些机器人不仅在技术上取得了飞速的发展，而且在
运动规划和稳定性控制方面也取得了显著的成就。
国内研究现状：中国在人形机器人产业的发展过
程中，经历了从追赶到领先的转变，其中创业企业
典型代表包括优必选科技、宇树、傅利叶等；高校
领域则以哈尔滨工业大学研制的GoRoBoT机器人、
清华大学研制的Stepper-2D机器人为代表。

5

研究现状 Research Status


02

# 项目方案

P r o j e c t P l a n


7

### 01 设计一套大型伺服双足机器人以供算法研

究使用

### 02 研究基于二维线性倒立摆的步态规划器

### 04 将网络模型迁移到现实机器人身上，进行

Sim to Real的行走实验

03

应用基于质心期望力的线性倒立摆所得到
的规划步态形成参考轨迹，使用强化学习
算法，在虚拟环境中迭代训练


03

# 项目实施进展

P r o j e c t P r o g r e s s

## 整体架构


## 机械结构——机械总论


## 机械结构——腿部结构仿生设计


人体腿部整体外形曲线呈上粗下细的倒三角 | 人体膝关节解剖图与机器人对应体

## 机械结构——轻量化设计


使用Altair Inspire进行二维拓扑优化

使用Altair Inspire进行三维拓扑优化

## 机械结构——实物展示


## 硬件设计——整体框架


整体框架

核心板原理图
核心板PCB图

核心板

核心板调试图

## 硬件设计——驱动部分


控制框图

速度环控制

九轴加速度计代码

关节控制代码

速度控制CAN协议代码与引脚配置

关节实物演示

## 神经网络框图


宇树模型强化学习训练 训练Reward

神经网络环境搭建


04

# 项目特色与创新

P r o j e c t f e a t u r e s a n d i n n o v a t i o n


18

### 01 极低的成本实现较强的运动性能

### 02 开源属性增加社群影响力

### 03 腿部关节以及计划足式仿生学设计


19

### 01 极低的成本实现较强的运动性能

### 02 开源属性增加社群影响力

### 03 腿部关节以及计划足式仿生学设计

上万浏览量，近百硕博交流

目前共知道三人开始复刻，有近10套
意向，但是可能不一定有空做

https://zhuanlan.zhihu.com/p/692264591


Thanks for watching!

# 感谢观看！

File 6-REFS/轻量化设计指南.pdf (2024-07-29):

# 写在前面

竞技机器人的重量对于机器人性能有至关重要的影响，在大多数情况下更轻的重量意味

着更大的极限速度、更高的加速性能、更快的动态响应与更高的效率，尤其是在 RoboMaster

这种存在功率限制的竞赛中，优秀的轻量化设计更是不可忽略的要点。

很多设计者认为“沉就是好，粗就是强”，这不能说完全错误，但至少是不适合竞技类

机器人竞赛的。竞技机器人，突出的就是一个“竞技”，想要从中脱颖而出，要的就是“极

限”。更极限的方案、更极限的性能、更极限的操作、更极限的稳定，这些共同作用才能有

一个更接近极限的结果。

本篇主要是讨论如何进行轻量化设计与减重，即“减重设计”和“零件减重”这两方面，

其中减重设计主要是设计思维层面的内容，本篇受篇幅所限不会过度展开，如果各位感兴趣

以后可以再出专门的篇章进行讨论。对于竞技机器人而言，各类型板材是占比最高的一类材

料，故本篇将着重讨论如何对板材进行减重。另外本篇的根本目的是“多快好省的教会读者

做一个还不错的减重设计”，并不追求完美，所以也就不会过多对减重理论进行阐述，如有

兴趣可以私下与我交流。

本篇中提供了一些在各种工况下使用的减重样例，望各位读者能思考其中的设计逻辑。

零件减重，尤其是板材减重，很重要的一个学习方式就是“多看”，通过对他人合理的减重

设计多分析、多思考能有效的快速提升自身的设计能力。本文档受篇幅所限，案理不算很多，

希望大家在读完后结合自身情况进行举一反三。

需要说明的是，本文档主要基于 RoboMaster 等竞技机器人比赛，与真实的非标产品设

计有所区别，请读者不要混淆。

哈尔滨工业大学 竞技机器人队
金子旭
2022.2.9

# 版本说明

2022.2.9 | 首次发布 | v1.0

## 一.减重，减哪里？

对于一台竞技机器人来说，减重的地方可以很多，例如最常见的板材掏减重孔、方管打

减重孔、打印件镂空等等，但在减重效果最好的无疑是在结构设计上的减重，换句话说，就

是“砍结构”，我们可以叫它“结构减重”。

举个例子，一台家用通勤摩托车需要减重，它的主要动力部分有发动机、油箱、传动系

统、轮系及轮胎，如果保持大体结构不变，只从动力部分做减重的话，那所能做的非常有限。

但如果换个思维，如果只是通勤用，那换成电动摩托车行不行，这直接砍去了近乎整个传动

系统，甚至可以直接使用轮毂电机，这样就可以直接省去大量的结构重量。这就是通过思维

的转换，尝试在大体实现目标需求的情况下通过实现方式的调整实现的减重。

当然，对于具体结构件上的减重设计还是有必要的可以管他叫“零件减重”，例如开减

重孔、减重槽、镂空等方式都可以实现一定程度的轻量化，但必须认识到的是，在大多数情

况下通过对零件进行减重设计所能带来的重量减少都是比较有限的，其是远不如直接“砍结

构”所带来的效果的。

综上所述，轻量化设计的思路应该是“砍结构为主，减材料为辅”的方式，即通过改变

实现方式省去冗余结构的方式进行主要的减重，并以对个体零件的镂空、更换低密度材料等

方式进行辅助，总体上实现竞技机器人的轻量化设计。

## 二.对于结构的减重

正如上面的例子所表现的，结构减重的根本是“对需求的分析”与“思维的转换”。这

部分有些抽象，不同设计者对它的理解也有所差别，但归根到底可以总结为，“从根源入手，

用最简单的方式，实现最需要的功能”。宁简勿繁，能实现功能就是好设计，在能实现功能

的基础上，越简单越好，多余的机构统统砍掉，也就是“砍结构”，这是实现整体轻量化最

直接，也是最快速的方式。

砍结构的前提是对于需求有着清晰的理解，很多设计者在设计机器的过程中都不知道自

己到底想要什么，这种“船到桥头自然直”的状态也就自然不可能对需求有清晰的认证，在

设计过程中产生些冗余也就十分正常了。要想避免这种糊里糊涂的设计，最简单的办法就是

找张纸，列一下几个优先级的需求，并画一画逻辑链（如果不知道是什么，请见‘结构设计

的思维逻辑’），捋清楚自己的需求。明确需求再设计，这是一个好设计的基础，也是简洁设

计的基础。

## 三.对于板材的减重

板材的减重是竞技类机器人中最常见的减重类型，也是本篇的重点。正如我在《结构设

计的思维逻辑》中所提到的，对板材减重的根本是“适可而止，够用就行”，换句话说就是

在满足使用要求和合理的冗余的前提下，能薄就薄，能抠就抠，尽量将材料性能发挥到极限。

我们不妨定义一个“减重比”，即减去的重量与损失的刚度的百分比的比值，用以大概衡量

减重设计的“性能”，减重比越大，说明减重设计越好，反之亦然。

3.1.减重孔种类

如果进行到抠减重的环节，那说明该板材零件的形态及孔位已经确定，接下来就要根据

受力形式及工况综合确定减重孔的形式。减重孔并只是“孔”，它有形态各异的样式与类型，

大体上，常见减重孔的形式及特点如下：


类三角形减重孔：


类三角形减重孔指的是形态类似于三角形的减重孔，换句话说它的边不一定是直的，可

能有一定的弧度或其他形态，但仍可保持大致的三角形轮廓。如下图左侧红框部分

这种减重孔比较适合梁状零件、多边形零件、环状零件、零件突出部的减重，例如用来

抗弯的悬臂梁等（上图右侧）。绘制此种减重孔的根本目标是尽量让载荷分布到零件内部的


力线尽量与内部支撑梁重合，也就是尽量让内部支撑梁处于二力杆的受力状态，另外需要根

据载荷和工况的不同调整不同支撑梁的粗细长短。

更多样例：


四边形减重孔：


四边形减重孔指的是形态近似于四边形的减重孔，这种减重孔多用于多个规则孔位中部

的减重，或是在受力较小的区域尽可能多的去除材料。

例如下图中左侧标蓝的板子的步兵侧面装甲板的安装板，我们简单分析受力可以知道，

由于这个板子与底盘框架固定的安装孔位在与装甲板固定的孔位的外侧，而装甲板与装甲板


支架又可以视为一个刚体，故其主要内应力应集中于内、外安装孔之间，即红框的区域，而

中部所承受的载荷很小，所以中间的基本所有区域都可以掏空，只留下很少的边条用来维持

基本形态以方便装配与布线，在实际测试中装甲板安装刚度也很理想。

需要注意的是，此类减重孔的边角处容易产生应力集中，不要忘记进行倒圆角等操纵。

更多样例：


多边形减重孔：

这里的多边形减重孔主要特指五边形减重孔和六边形减重孔的密集阵列，也就是所谓的

“蜂巢”，此类减重孔使用于非承力区域的大范围减重，例如舱盖、底板中部、背板等区域。

此类减重孔的一大特点就是受力均匀，但不善承受冲击，故不太适合用于外表面的防护

材料。举个例子，若把一块切割的很极限的蜂巢减重板作为作为 RoboMaster 竞赛中的弹丸

防护板，那如果被大弹丸正面击中，纤细的支撑难免断裂，就会破坏原本均匀的承力结构。

这时候可能有同学会问了，“那我把支撑梁画粗一点，六边形之间的大一点不就好了吗？”，

但这就十分尴尬了，蜂巢减重的目的是追求在非承力区域尽量轻一点（当然还有美学目的），

如果只是为了求结实，为什么不用几个简单的三角形减重支撑结构，再贴块胶布防止弹丸进

入呢？所以说，既然要用蜂巢，就不要背离本质需求，把蜂巢搞成了“六边形的离散减重孔”

（如下右图），在一些约束条件下，蜂巢减重是有其独特的优势的，但这需要根据不同的情

况具体问题具体分析，还是那句话，没有正不正确，只有合不合适。

圆形减重孔：


圆形减重孔是最“传统”的减重孔，工艺性也是几种减重孔中最好的，用钻头/开孔器

就可以简单实现。这类减重孔常用于方管、非承力板材的减重。

圆形减重孔的一大特点就是受力均匀，且减重的程度幅度相当可观，例如在大口径的铝

方管减重案例中，应用合理的圆形减重孔可以使铝方管同时在两个方向有不错的抗弯、抗压

性能，且减重幅度和精心设计过的三角形减重也差不太多，工艺还十分简便，是竞技机器人

中铝方管减重的首选。


还有一种情况，便是应用于一些环状零件的减重上，多为齿轮、链轮等传动部件的减重。

槽形减重孔：

槽形减重孔是我很喜欢的一类减重孔，因为它贯彻了“适可而止，够用就行”的理念。

它常用于线性与环形零件的减重，比如连杆、线轨、齿轮、链轮等零件，也可用于非承力的

板材，对其进行比较极限的密集减重。样例如下：


类多边形减重孔：

类多边形减重孔是最“科学”的一类减重孔，它的指的通过对零件的载荷进行分析，融

合多种减重孔类型，以最少的材料实现承受载荷的需求。此类减重孔形式多种多样，但核心

宗旨是尽量让载荷的力线与内部支撑结构的走向一致，同时满足避开移动部件轨迹、电气走

线等需求，比如下图：

如何绘制此类减重孔会在 3.2 部分中重点讨论，此处不做赘述。虽然此类减重孔性能最

好，但相对的绘制比较麻烦，所以在一些规则零件受到简单载荷时更多的还是采用前文所提

到的几种规则减重形式进行处理，只有在孔位较多、受力较复杂、或有其他需求（如美学需

求）等情况下才会使用此种类多边形减重孔。另外关于有限元分析软件与拓扑分析的部分会

在 3.4 中进行讨论，此处也就不再赘述了。

更多样例如下：

3.2.怎么抠？抠多少？

在完成对板材轮廓和孔位的设计之后，就可以对其进行减重的操作了。具体怎么设计减

重孔是个复杂且综合的过程，每个设计者都有不同的理解，但不论是怎样风格的设计者，都

免不了对板材受力情况与外部约束条件进行分析，此处的“约束条件”不单纯指力学上的约

束，也指使用环境上的，例如是否需要从孔中走线、是否要防止弹丸进入、是否要考虑美学

需求等。大体上，设计减重孔可以分为 5 个步骤：

下面我来对这几步逐个说明：

分析：

我一向认为，设计最重要的阶段是设计前的思考，对于减重设计而言，即是思考各载荷

与力学约束条件之间所产生的力的大小与方向，以及这些力的种类特点。此时对受力的方向、

大小、类型以及特点有清晰的认知可以对后续“分割”阶段具体的减重孔的设计提供重要的

帮助，从而明确到底该在那个区域使用哪种减重孔形制。

例如在 RoboMaster 2021 赛季 I HITer 国赛版本的工程机器人中，由于是“平行四边形

连杆+夹爪”的方案，且对矿石 pitch 轴调整电机在夹爪末端，这就造成夹爪执行器末端质

量偏大。考虑到取矿对效率要求较高，夹爪执行器的质量应该是越小越好，更小的质量能有

效提高夹爪机构的响应速度，这就要求夹爪机构的轻量化。同时由下图的结构可以知道，夹

爪结构主体会承受“横向”“纵向”两个方向的载荷，所以此处主体减重孔形式采用了三角

形桁架的形式，并在纵向上设置桁架插板来增强结构的抗弯性能，提升结构的刚度。原则上，

尽可能的让分力方向与内部支撑的走向一致。


在受力分析中，可以大致的将零件分为“主承力区”“辅助承力区”“不承力区”，在此

阶段的划分可以是模糊的，停留在思维上就好，在后续的“分割”步骤中会详细区分，原则

上承力区越重要，其支撑材料越多，越需要加强。

留边：

各位读者对杠杆原理应该都所有了解，动力臂越长，阻力臂越短，也就越省力，类似的

在材料力学中有中性轴的概念，零件的应力分布随与中性轴的距离越远逐渐增大。换句话说，

如果载荷一定，结构越大（即边缘与中性轴距离越远）材料所受的最大应力越小。这一点对

应到减重设计上，即是“越靠边缘越重要”，换句话说，边缘的结构所承受的力要比零件中

心区域更大，也就需要更多的材料、更强的结构来进行支撑。当然，这并不绝对，需要根据

设计、载荷具体情况具体分析，但边缘更为重要的这一结论仍适合于大多数工况。

对应到具体操作上，也就是在绘制具体减重孔之前先将边缘根据载荷情况留出边条，分

割出中间受力不大的“辅助承力区”进行减重的操作。

分割：

这一步是将零件的“辅助承力区”进行进一步的分割，并根据载荷与工况留出支撑结构

后将剩余部分去除。具体如何分割很难有定式，但大体上遵循以下规则：

a.最短距离原则

减重设计的根本目的是“在去除尽量多材料的同时保留尽量高的刚度”，而我们知道任

何结构只要长度过长，刚度必然下降，这对于支撑结构也一样，所以所谓“最短设计原

则”即是指在已经确定支撑结构的起始位置后，在各个可能的支撑结构中选择最短的那

个。例如下图，左侧的设计就优于右侧。


b.三角支撑原则


我们知道三角形是多边形里最稳定的结构，而在辅助承力区分割的这个操作我们也可以

看作是将一个不规则多边形进行分割，且要求内部结构的稳定，这样看在孔位分布允许

的条件下，尽可能的将区域分割为三角形无疑可以增强结构的稳定性，当然一味的增加

三角形会导致减重效果不佳，这需要与“最短距离原则”与“宁简勿繁原则”综合考虑。

c.孔位优先原则

零件上的孔位需要优先确定，先定孔位，再开减重。这些孔位非常重要，需要依靠他们

与其他零件进行连接，换句话说它们就是零件机械上的约束，在分割过程中无比需要保

证承力的孔位的附近有足够好的强度，足以承受住载荷并传递过去。但很不幸，不是所

有孔位的分布都适合开减重孔，所以也就在开完减重孔之后出现了“无家可归”或是位

置非常奇怪的孔位，这可不太好。下列是一些对于不同奇怪孔位处理的样例：

d.宁简勿繁原则


减重区域的支撑路线的选择并不唯一，这需要结合实际情况具体考虑，但在没有特殊需

求的前提下，我认为在满足使用需求的前提下，减重孔的支撑结构应该尽量简单，正如

奥卡姆剃刀理论所描述的那样，若无必要，勿增实体。对于减重形式的选择而言，也就

是“在满足需求的前提下，最简单的模式才是应该选择的模式”。

切除：

在完成了减重形式的设计后，将计划去除的区域切除即可。这个步骤在建模软件有多种

实现的方式，有的设计者喜欢直接在同一草图中进行完整的草图绘制，也有的设计者偏好先

切出外支撑轮廓，然后再构建内部支撑。不同的建模方式没有好坏之分，只要能符合自身的

使用喜欢，达到自身使用下的最高工作效率即可。

后处理

本部分的后处理指的是设计阶段的后处理，包括倒角、倒圆角以及增加挂耳（辅助布线）

等，其中倒角半径的选择应与支撑梁的倾斜角度相关，详细关系将在 3.4.b 中详细说明。

3.3.关于有限元仿真

随着技术的发展，有限元仿真在设计中的占比越来越大，在项目中越发频繁的利用各种

仿真手段来模拟真实载荷与工况，用以对设计进行反馈。但是，对于以 RoboMaster 为代表

的各类竞技机器人比赛而言，仿真也有它的局限性，其中最大的局限便是与竞赛设计的低要

求、与开发周期的矛盾以及相关约束条件的缺失。

实话实说，竞技机器人对于设计的要求是很低的，做不到极致的轻量化高强度？没关系，

那就加点冗余嘛；做不到高效的自动化控制？没关系，那就操作手多费点心嘛；做不到很高

的可靠性？没关系，还可以靠队友补救嘛。低门槛、高上限的特点就造成了竞技机器人比赛

“技术主导”的特点，但要注意的是，技术也是分权重的。例如对 RoboMaster 比赛而言，

视觉自瞄的好坏就远比怎么画减重更为重要，也更直接的能影响一场比赛的胜负。

正是由于比赛“又不是不能用”的这一特点，对于大多数队伍来说，在紧张的研发周期

中拿出可观的时间利用有限元技术去分析一个零件的减重，并不是一件很划得来的事，经常

会出现“我们花费数个小时，成功的把这块板材从原减重方案的 100 克减重到了 90 克”的

情况，对于大多数竞技机器人的需求而言，真的差这 10 克吗？更何况由于约束条件的不完

整，绝大多数仿真的精度也算不上高，仅能提供一定的指导性反馈，这对于有经验的设计者

意义十分有限。

但客观来说，仿真软件的意义依然是巨大的。不论是前期的方案论证、虚拟样机的低成

本快速迭代还是拓扑分析对于减重方案的指导这都是有巨大意义的，只是他并不适合竞技机

器人大批量低要求板材的减重设计。

3.4.一点心得

a.勿忘倒角

经过减重设计后的板材难免出现一些拐角，这时候倒角操作就很有必要。对于板材内部

的折角，倒角不但可以缓解应力分布，防止应力集中，也可以优化工艺性；对于外轮廓的倒

角则主要是为了机器人操作者的安全，毕竟谁都不希望开开心心上班来，满手伤痕回家去。

在设计上，每个倒角的形式于半径大小需要根据情况而定，但我个人偏好在内外轮廓的

直角拐角处使用倒边，斜角拐角处使用倒角，这在保证性能的同时也具有美学特性，线条感

可以使零件的力量感更强，更具有设计美学。比如下图，左图明显比有图更具有设计感与力

量感，在外轮廓边角上倒边也能减去更多的重量。


b.圆角半径大小与倾斜角度相统一


如果倒角的支撑结构不垂直（如下图），则需倒角的角 1 和角 2 就需要采用不同的圆角

半径，一般认为夹角越小，所需的圆角半径也越小，夹角越大，所需的圆角半径也就越大。

当然，最小半径也需要根据机床的刀具尺寸结合具体情况综合确定。


c.不要刻字

我是十分反对在板材上镂空刻字的，除非有一些特殊的美学需求，否则对于板材是刚度

有很大的负面影响的，而且字体内部的尖角还存在翘起后刺伤使用者的安全隐患，而且更为

重要的是，这也不好看啊，合理设计的减重支撑、充满力量感的边线、流畅圆滑的轮廓无不

自然带有设计的美感，真的不需要再画蛇添足了。如果有内容上的需求，可以选择定制不干

胶贴纸，或是板材浮雕加涂料，高对比度的效果更为突出，在大体保留结构性能的同时还能

突出内容，效果远胜于镂空刻字。下面是一些反面教材：


## 四.对于立体零件的减重

4.1.思维逻辑

立体零件是竞技机器人中另一类经常使用的零件，例如各型铝方管、3D 打印件以及各

型机加工件，此类零件多种多样，载荷情况也五花八门，受体量所限本篇也不可能详细阐述

每一种零件的减重方式，故本部分仅会阐述相关的思维逻辑，对详细的操作不会过多提及。

客观上，立体零件除了铝方管外，其他种类的零件在竞技机器人中使用的比例并不高，

且由于其结构的立体性与复杂性，对其设计减重的“减重比”也并不大，可谓是费力不讨好。

而且受限于经费，各参赛队伍所用的加工件也都“惜件如金”，其往往都作为关键零件来承

受关键载荷，过分减重也不利于冗余性的考量，所以我个人不太建议在机加工零件上过分减

重。当然，这仅限于由铝合金等轻金属材料制成的关键工件，至于材料是钢铁的零件减重还

是十分必要的。

在思维上，可将立体的工件才分为多个“面”，也就将其“降维”，从三维的复杂零件转

化成多个二维板面，再对面进行减重，此时的操作就与上文中对于二维板材的操作十分类似

了。但需要注意的是，3D 打印的材料由于特性原因，又与单纯的“开减重孔”不太一样，这

部分可以详见 4.3 的内容。

4.2.对于机加工件

机加工件的形态多种多样，很难一概而论，但究其根本都是将应力分布较低的区域去除，

通过去除材料的方式来降低总体质量。当然，去除材料的同时不要忘记考虑工艺性，良好的


工艺性能在相当程度上降低成本。样例如下：

4.3.对于 3D 打印件

打印件按工艺不同可以分为 FDM、SLA 和粉末烧结三大类，工艺的不同带来了它们不同

的性能特点，而这对应到减重上又使它们有着不同的方式。

FDM 减重的花样比较多，可以有改变填充率、掏减重孔、填塞加强材料等多种方式来实

现轻量化的目的。改变填充率顾名思义，就是通过改变填充的百分比来改变材料，就不再赘

述了；掏减重孔也就如同字面意思，但需要注意的是，对于 FDM 的打印件来说，减重孔的切

除方向尽量和打印的堆层方向垂直，否则打印件容易层间开裂；填塞加强材料的操作比较有

趣，是将圆柱销、碳棒、碳管等作为加强材料塞入打印件内，从而将其他部分的材料去除，

即用少量高强度材料替换大量低强度材料。填塞的方式也可以用于打印件的结构增强。


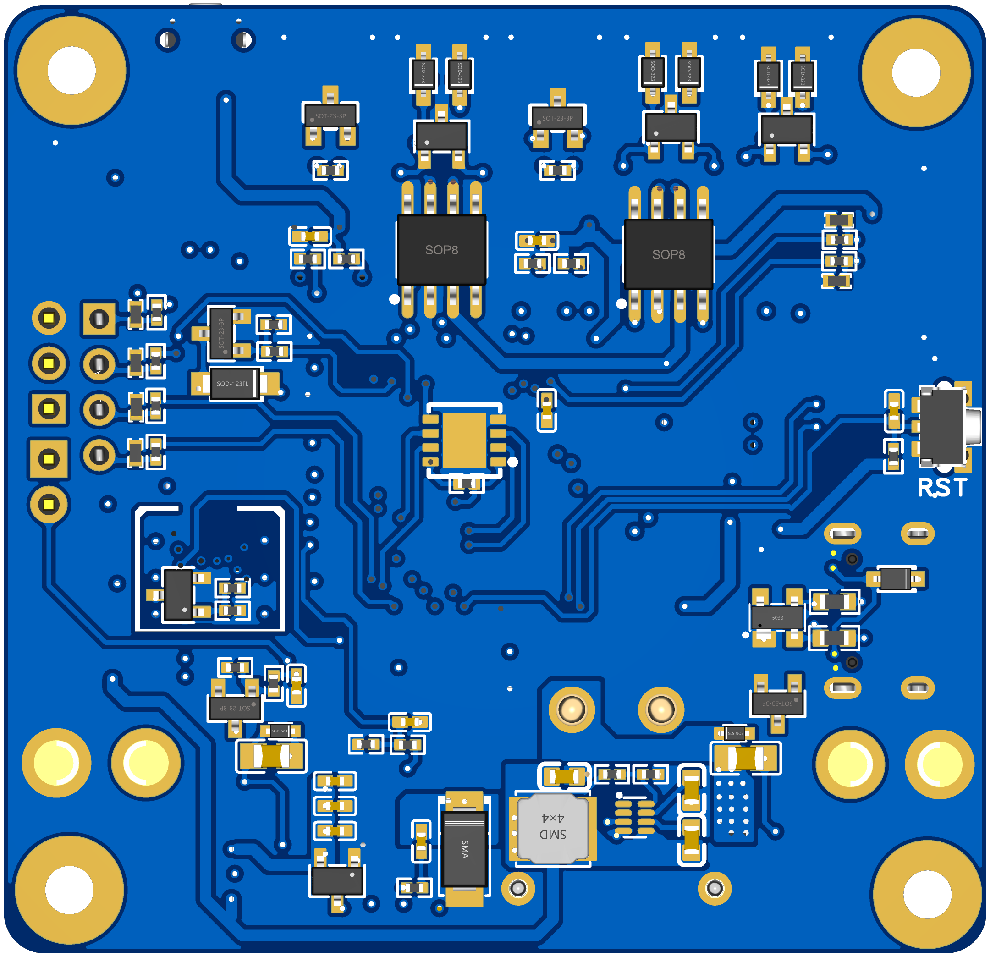
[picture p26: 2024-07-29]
1-Hardware(PCBS)/STM32H723(Now_Using)/3D_PCB_back.png

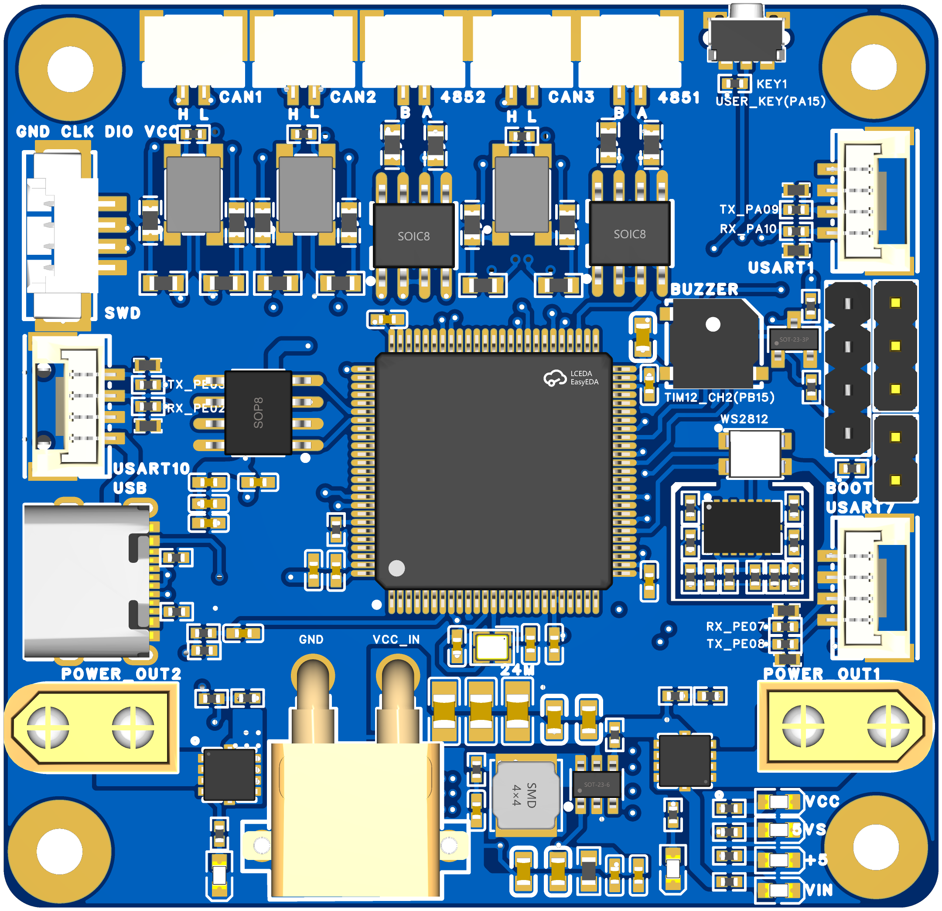
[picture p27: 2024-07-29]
1-Hardware(PCBS)/STM32H723(Now_Using)/3D_PCB_front.png

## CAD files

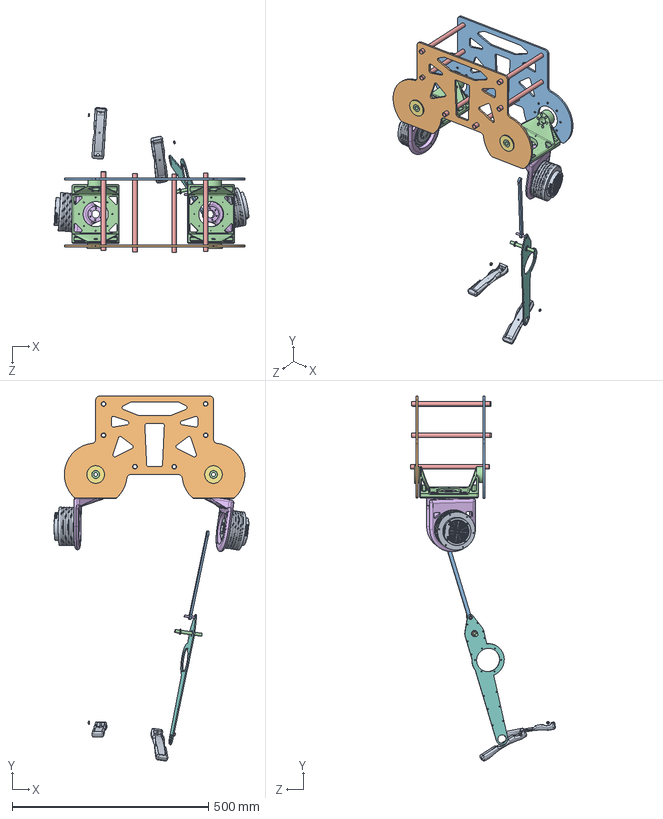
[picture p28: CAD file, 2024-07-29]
4-ModelsV1/AlexbotV1/人形机器人V1.4.SLDASM
496.1 x 929.6 x 368.9 mm
前板1
背板1
TOF1输出件&TOF2固定件 x 2
碳管支撑 x 6
TOF2输出件&TOF3固定件 x 2
DM-J8009 x 2
内20外42法兰轴承 x 2
左小腿内板
足底 x 2
M4防松螺母 x 2
拉杆
M8双头螺丝
内8外14高4推力球 x 2
M5-16双头螺丝

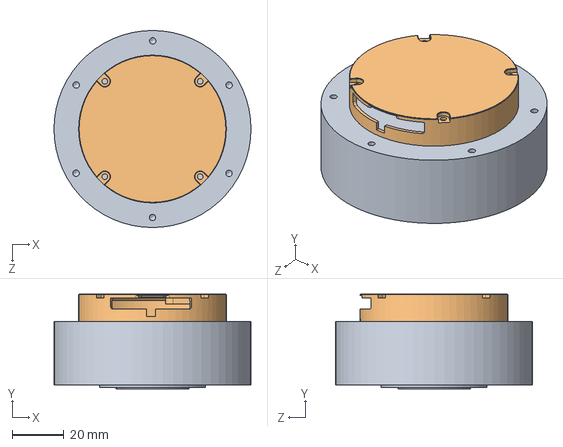
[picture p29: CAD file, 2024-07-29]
4-ModelsV1/AlexbotV1/电机文件/DM-J6006.SLDASM
76.0 x 36.5 x 76.0 mm
DM 6210 3D
6210 减速电机驱动板盖

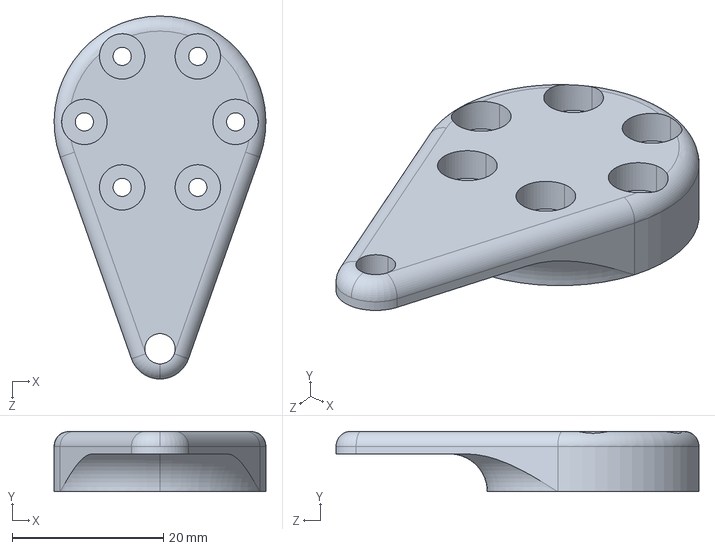
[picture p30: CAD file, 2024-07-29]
4-ModelsV1/AlexbotV1/加工文件/1-CNC加工/1 DMJ6006电机连接件（加工两个）.STEP
28.0 x 8.00 x 48.0 mm

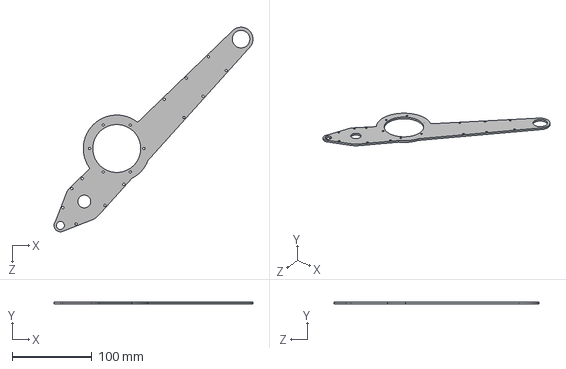
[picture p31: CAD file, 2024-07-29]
4-ModelsV1/AlexbotV1/加工文件/2-碳板切割/3 左小腿内板.STEP
249.5 x 3.00 x 256.6 mm

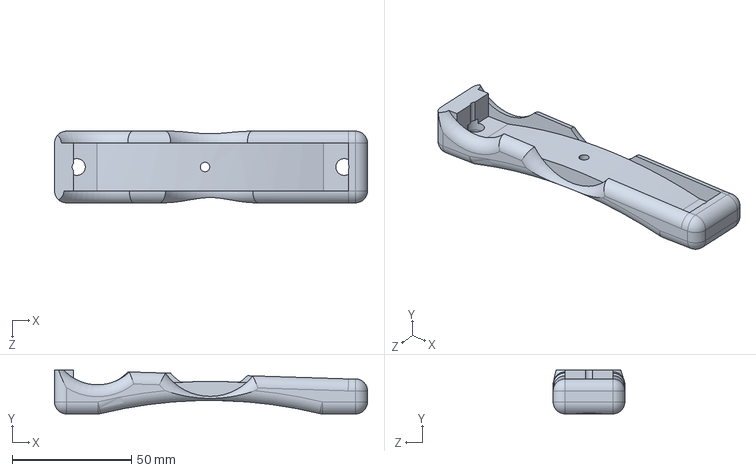
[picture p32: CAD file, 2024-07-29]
4-ModelsV1/AlexbotV1/加工文件/3-软胶加工/足底.STEP
131.0 x 18.3 x 30.0 mm

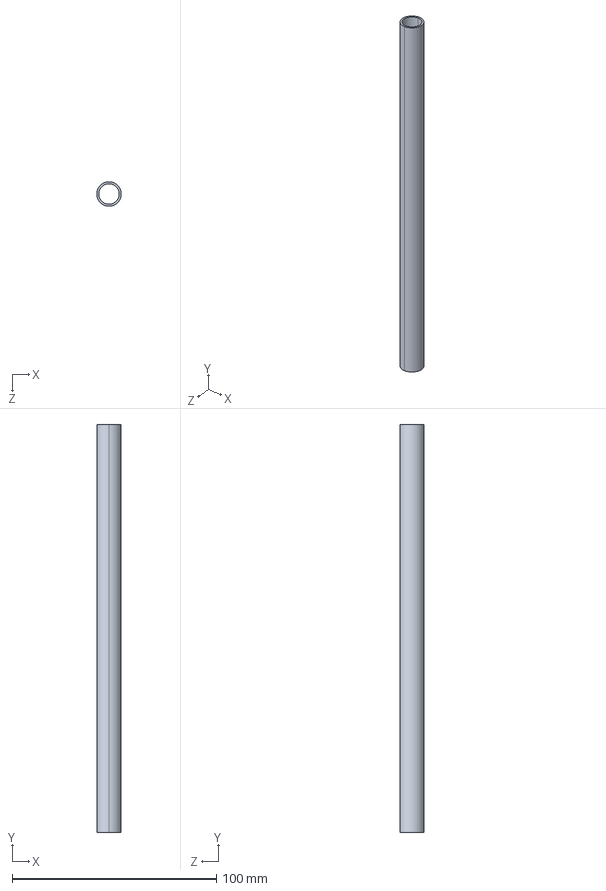
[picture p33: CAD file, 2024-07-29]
4-ModelsV1/AlexbotV1/加工文件/4-碳管/内10外12长200碳管六根.STEP
12.0 x 200.0 x 12.0 mm

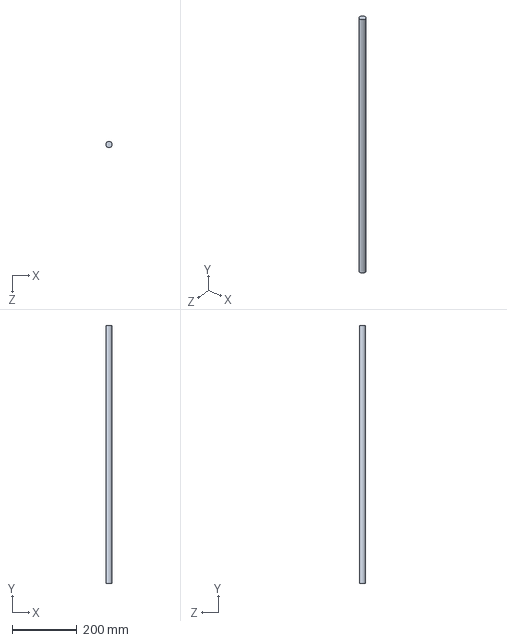
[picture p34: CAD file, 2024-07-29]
4-ModelsV1/AlexbotV1/标准件/测试件.SLDPRT
20.0 x 800.0 x 20.0 mm

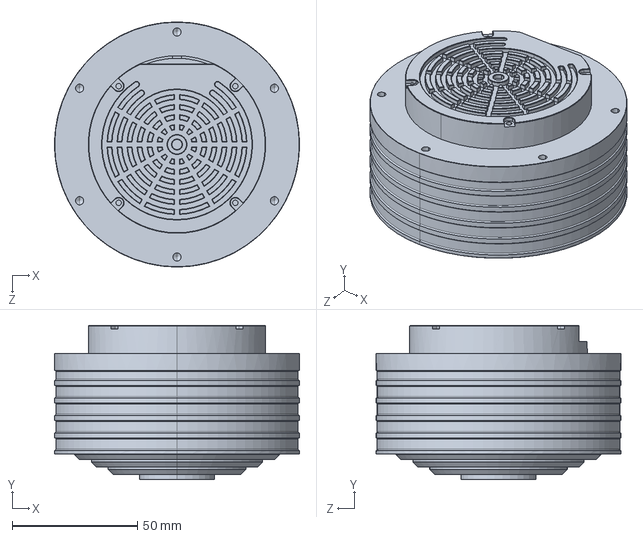
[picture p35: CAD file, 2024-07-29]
4-ModelsV1/AlexbotV1/电机文件/DM-J8009.SLDPRT
98.0 x 61.7 x 98.0 mm

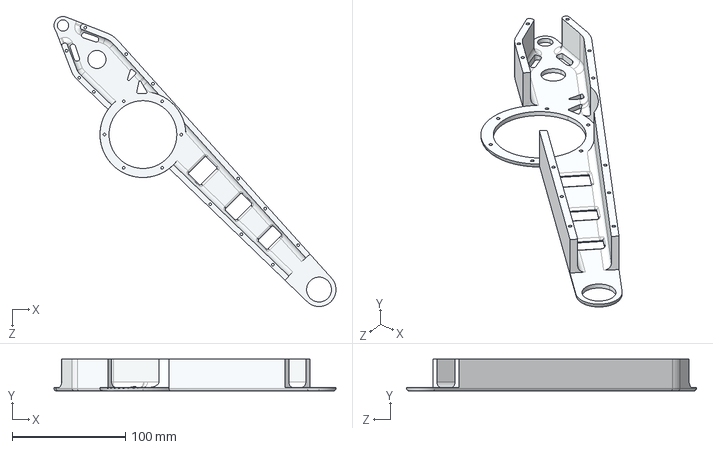
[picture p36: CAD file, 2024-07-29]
4-ModelsV1/AlexbotV1/加工文件/1-CNC加工/7 右小腿外板.STEP
249.5 x 28.0 x 256.6 mm

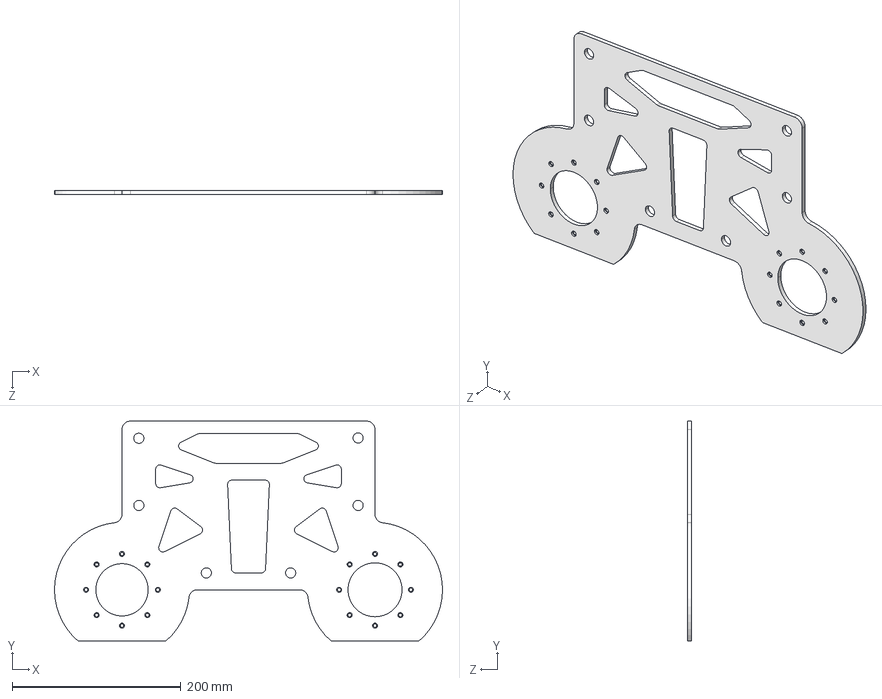
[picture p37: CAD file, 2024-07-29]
4-ModelsV1/AlexbotV1/加工文件/2-碳板切割/1 背板1.STEP
460.0 x 260.6 x 5.00 mm

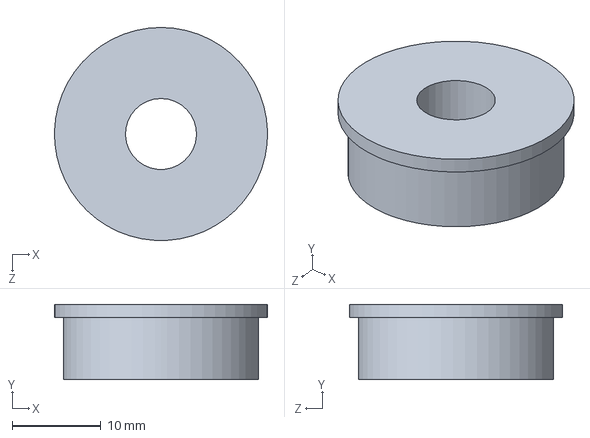
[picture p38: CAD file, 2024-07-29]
4-ModelsV1/AlexbotV1/标准件/内8外22法兰轴承.SLDPRT
24.0 x 8.50 x 24.0 mm

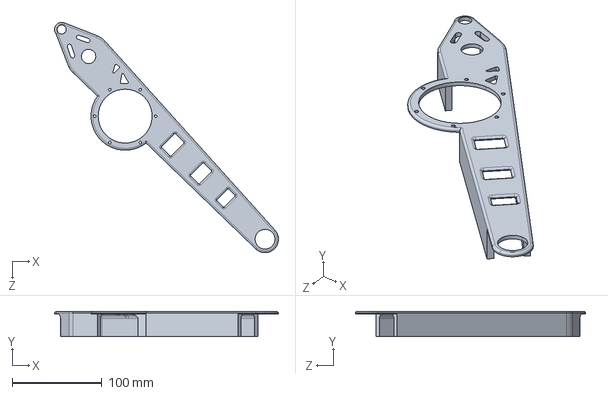
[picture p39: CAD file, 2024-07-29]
4-ModelsV1/AlexbotV1/加工文件/1-CNC加工/8 左小腿外板.STEP
249.5 x 28.0 x 256.6 mm

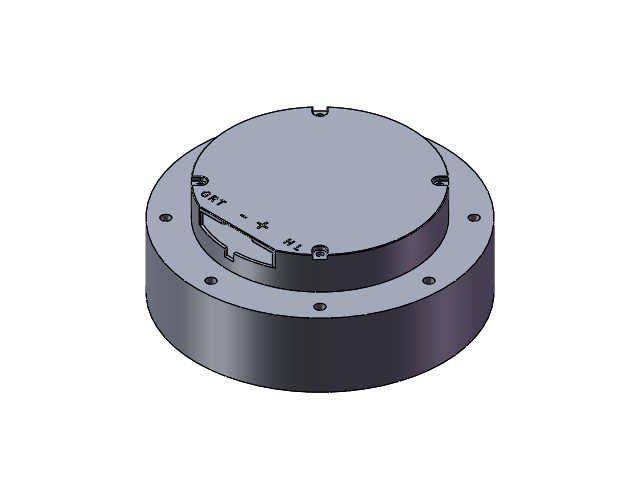
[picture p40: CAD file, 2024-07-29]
4-ModelsV1/AlexbotV1/电机文件/DM-J8006.SLDASM
DM 8108 3D
8108 减速电机驱动板盖

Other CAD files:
4-ModelsV1/AlexbotV1/加工文件/1-CNC加工/1-工程图/9 足端.DWG
4-ModelsV1/AlexbotV1/加工文件/1-CNC加工/1-工程图/4 TOF2输出件.DWG
4-ModelsV1/AlexbotV1/电机文件/DM 8108 3D.SLDPRT
4-ModelsV1/AlexbotV1/加工文件/1-CNC加工/1-工程图/5 大腿右.DWG
4-ModelsV1/AlexbotV1/加工文件/2-碳板切割/4 右小腿内板.STEP
4-ModelsV1/AlexbotV1/DM-J6006电机连接件.SLDPRT
4-ModelsV1/AlexbotV1/DM-J8006电机延长件短.SLDPRT
4-ModelsV1/AlexbotV1/M5-16双头螺丝.SLDPRT
4-ModelsV1/AlexbotV1/M8双头螺丝.SLDPRT
4-ModelsV1/AlexbotV1/TOF1输出件&TOF2固定件.SLDPRT
4-ModelsV1/AlexbotV1/TOF2输出件&TOF3固定件.SLDPRT
4-ModelsV1/AlexbotV1/内8外14高4推力球.SLDPRT
4-ModelsV1/AlexbotV1/前板1.SLDPRT
4-ModelsV1/AlexbotV1/加工文件/1-CNC加工/1-工程图/1 DM-J6006电机连接件.DWG
4-ModelsV1/AlexbotV1/加工文件/1-CNC加工/1-工程图/10 足端连接件.DWG
4-ModelsV1/AlexbotV1/加工文件/1-CNC加工/1-工程图/2 DM-J8006电机延长件短.DWG
4-ModelsV1/AlexbotV1/加工文件/1-CNC加工/1-工程图/3 TOF1输出件.DWG
4-ModelsV1/AlexbotV1/加工文件/1-CNC加工/1-工程图/6 大腿左.DWG
4-ModelsV1/AlexbotV1/加工文件/1-CNC加工/1-工程图/7 右小腿外板.DWG
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

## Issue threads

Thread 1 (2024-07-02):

如何做一个动物形状的对话robot

2m897, 2024-07-02:
如：和哆啦A梦 speak English

2m897, 2024-08-11:
要制作一个动物形状的对话机器人，您可以参考以下几个步骤：

1. **概念设计**：首先确定您想要的动物形状和机器人的功能。这将帮助您规划机器人的外观、大小和所需的技术规格。您可以参考一些现有的动物形状机器人案例，如仿生鸟或蛇形水下机器人等，它们不仅外观模仿动物，还能模拟动物的某些行为。

2. **技术选型**：根据您的设计概念，选择合适的硬件和软件。硬件可能包括电机、传感器、微控制器等。软件方面，您需要一个能够处理自然语言并进行语音识别和语音合成的平台。

3. **构建机器人的身体**：使用适当的材料构建机器人的身体，这可能需要一些工程技能。您可以使用3D打印技术来创建复杂的动物形状部件。

4. **编程和集成**：开发机器人的控制系统，集成语音识别和语音合成模块。您可以使用开源软件和硬件平台，如Arduino或Raspberry Pi，来编写控制代码和集成AI功能。

5. **AI集成**：利用AI技术，如自然语言处理(NLP)，来使机器人能够理解和响应人类的语言。您可以使用现有的API或开发自定义的AI模型来实现对话功能。

6. **测试和优化**：在制作过程中不断测试机器人的功能，确保其能够正常工作并优化其性能。

7. **外观设计**：最后，为您的机器人添加最终的外观设计，这可能包括喷漆、添加装饰或使用特殊材料来增强其动物特征。

例如，您可以使用AI驱动的动画制作工具——Artflow ai，来创建动物角色并生成动画视频，其中动物角色能够开口说话，这可以作为对话机器人的视觉部分。另外，LivePortrait是一款高效的肖像动画工具，它能够将静态动物图像转换为动态视频，适合需要从静态图像生成动态视频的用户。

请注意，创建一个动物形状的对话机器人是一个复杂的项目，需要跨学科的知识和技能。如果您是初学者，可能需要从简单的项目开始，逐步学习和积累经验。

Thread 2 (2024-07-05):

如何制作一个装修机器人

2m897, 2024-07-05:
刷墙 安装马桶

2m897, 2024-07-05:
如需融资 可联系 13024109369

2m897, 2024-08-11:
制作一个装修机器人是一个复杂且需要多学科知识的过程，涉及机械工程、电子工程、计算机科学和人工智能等领域。以下是创建装修机器人的基本步骤：

1. **需求分析与规划**:
  - 确定装修机器人的功能和性能指标，如自动搬运材料、墙面刷漆、地板铺设等。
   - 考虑机器人的工作环境，比如室内空间大小、地形复杂度等。

2. **设计机械结构**:
  - 根据功能需求设计机器人的机械结构，包括移动平台、执行器（如手臂）、夹具或工具头等。
   - 选择合适的驱动器，如电机和伺服机构，确保机器人有足够的力量和精度。

3. **电子控制系统**:
  - 设计电路和选择传感器，例如距离传感器、角度传感器、力矩传感器等，以实现精确控制。
   - 开发嵌入式系统，用于接收指令、处理数据并控制机器人的运动。

4. **软件编程与算法开发**:
  - 编写控制软件，管理机器人的各项任务和运动。
   - 开发路径规划和避障算法，使机器人能在复杂环境中自主导航。
   - 若需进行特定装修操作，如刷漆、铺砖等，还需开发相应的作业算法。

5. **人工智能集成**:
  - 如果机器人需要具备更智能的功能，如通过视觉识别环境或理解人类指令，可以集成机器学习和图像处理技术。
   - 使用深度学习训练模型来提高机器人对环境的适应性和决策能力。

6. **系统集成与测试**:
  - 将机械结构、电子控制系统和软件整合到一起，构建完整的机器人系统。
   - 进行初步测试，调整参数，优化系统性能。

7. **用户界面与交互**:
  - 设计用户界面，方便用户输入指令和监控机器人状态。
   - 开发人机交互系统，允许用户通过语音、手势等方式与机器人沟通。

8. **安全与合规性检查**:
  - 确保机器人符合相关的安全标准和法规要求。
   - 在机器人上设置紧急停止按钮和其他安全特性，防止意外伤害。

9. **实地测试与迭代改进**:
  - 在实际的装修环境中测试机器人，记录问题并不断优化。
   - 根据反馈调整硬件设计和软件算法，提升机器人的稳定性和可靠性。

10. **生产与部署**:
   - 完成原型机后，开始小规模生产。
   - 部署机器人到实际装修现场，进行工作，并继续收集使用数据进行产品迭代。

总之，这个过程需要跨领域专家的合作，以及大量的研发时间和资金投入。另外，随着技术的不断发展，装修机器人的性能和智能化水平也将不断提高。

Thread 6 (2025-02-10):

您好，我想学习，可以拉我进群或者给个联系方式吗

CSCB, 2025-02-10:
（づ￣3￣）づ╭❤～

Alexhuge1, 2025-02-10:
okok 我的wechat alex13917177320

---原始邮件---
发件人: ***@***.***&gt;
发送时间: 2025年2月10日(周一) 下午5:49
收件人: ***@***.***&gt;;
抄送: ***@***.***&gt;;
主题: [Alexhuge1/Alexbot] 您好，我想学习，可以拉我进群或者给个联系方式吗 (Issue #6)

（づ￣3￣）づ╭❤～

—
Reply to this email directly, view it on GitHub, or unsubscribe.
You are receiving this because you are subscribed to this thread.Message ID: ***@***.***&gt;

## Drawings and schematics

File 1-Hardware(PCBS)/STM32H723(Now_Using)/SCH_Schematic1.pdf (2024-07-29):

VDD 50 PB12 51 PB13 52 PB14 53 PB15 54 PD8 55 PD9 56 PD10 57 PD11 58 PD12 59 PD13 60 PD14 61 PD15 62 PC6 63 PC7 64 PC8 65 PC9 66 PA8 67 PA9 68 PA10 69 PA11 70 PA12 71 PA13 72 VCAP 73 VSS 74 VDD 75 PA14 76 PA15 77 PC10 78 PC11 79 PC12 80 PD0 81 PD1 82 PD2 83 PD3 84 PD4 85 PD5 86 PD6 87 PD7 88 PB3 89 PB4 90 PB5 91 PB6 92 PB7 93 BOOT0 94 PB8 95 PB9 96 PE0 97 PE1 98 VSS 99 VDD 100

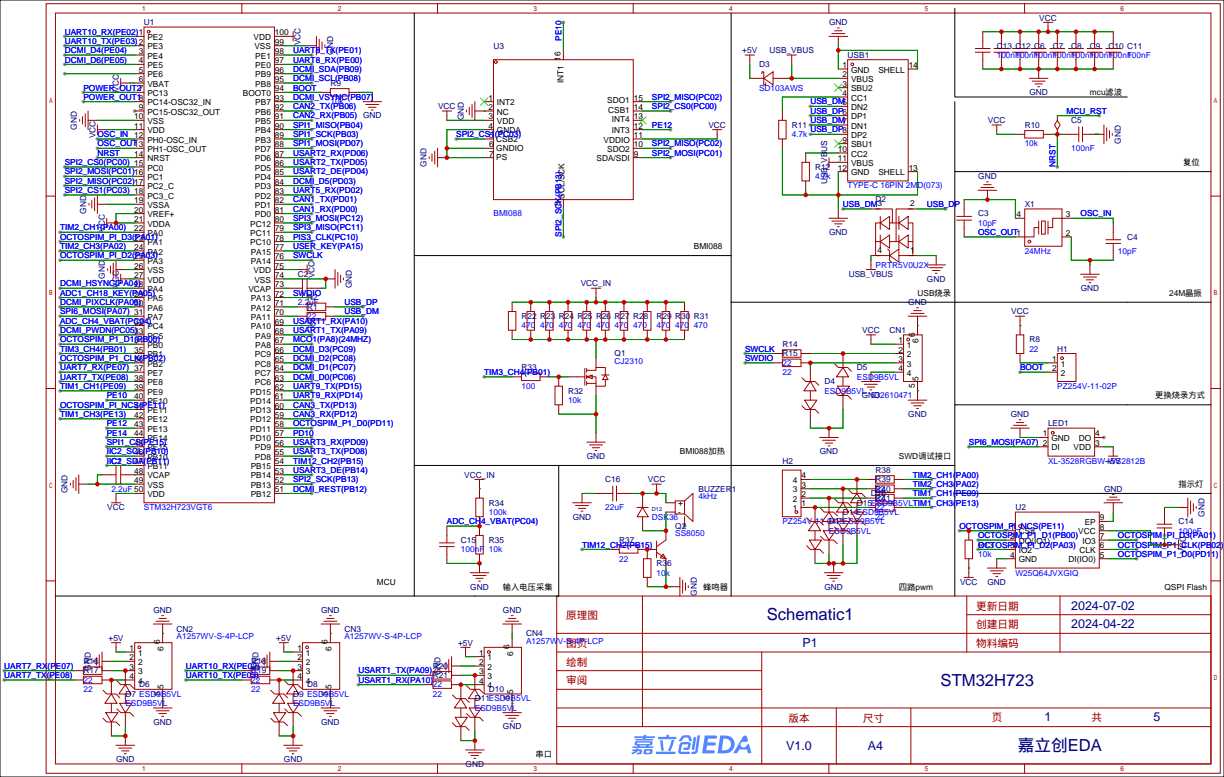
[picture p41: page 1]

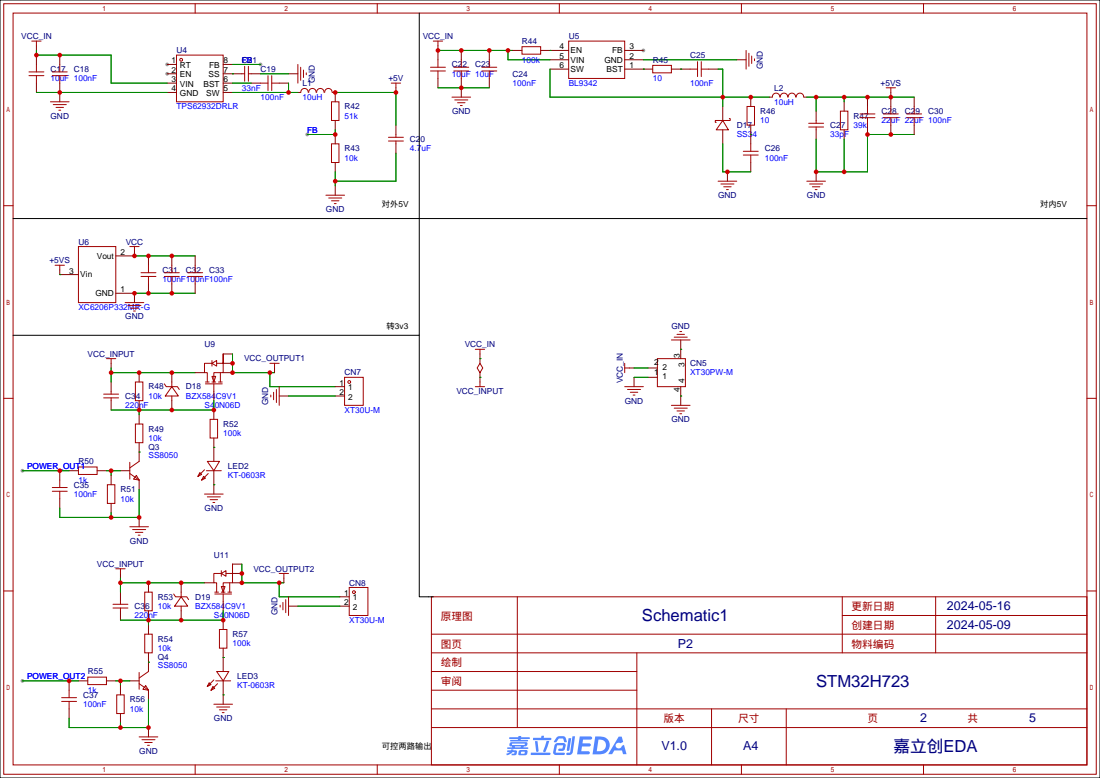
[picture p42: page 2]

# CAN2_RX(PB05) +5VS ⁺⁵VS +5VS

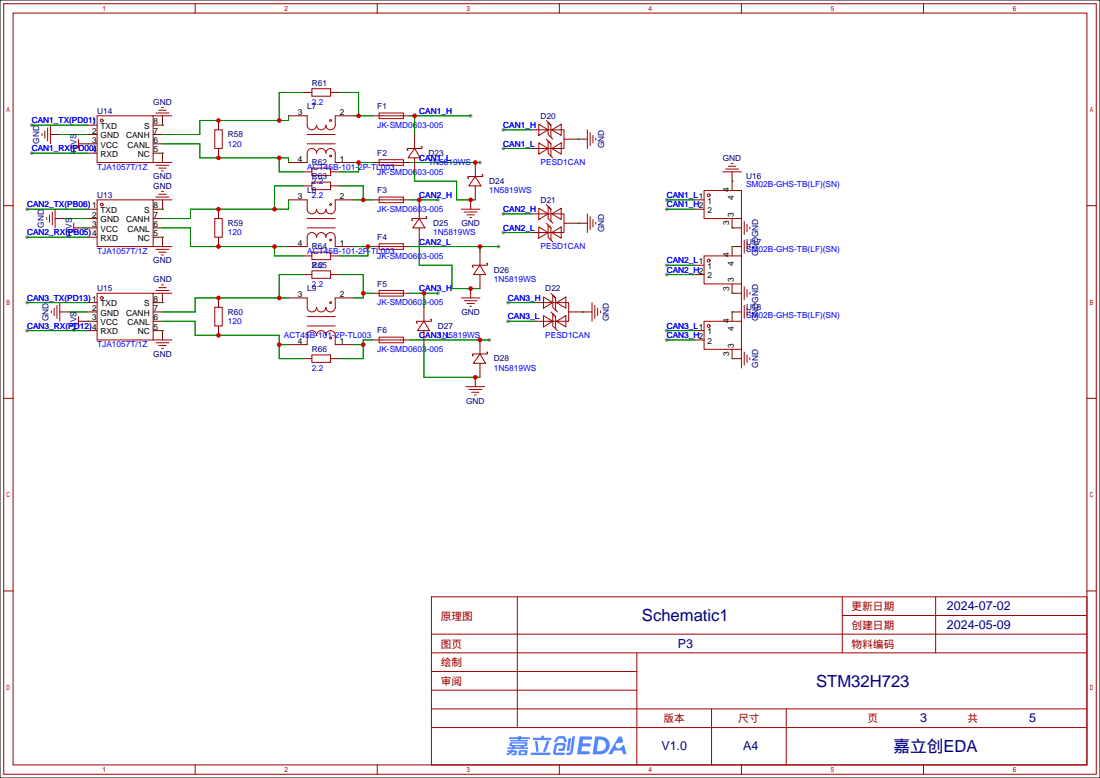
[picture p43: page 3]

GND GND GND GND GND
SM02B-GHS-TB(LF)(SN)

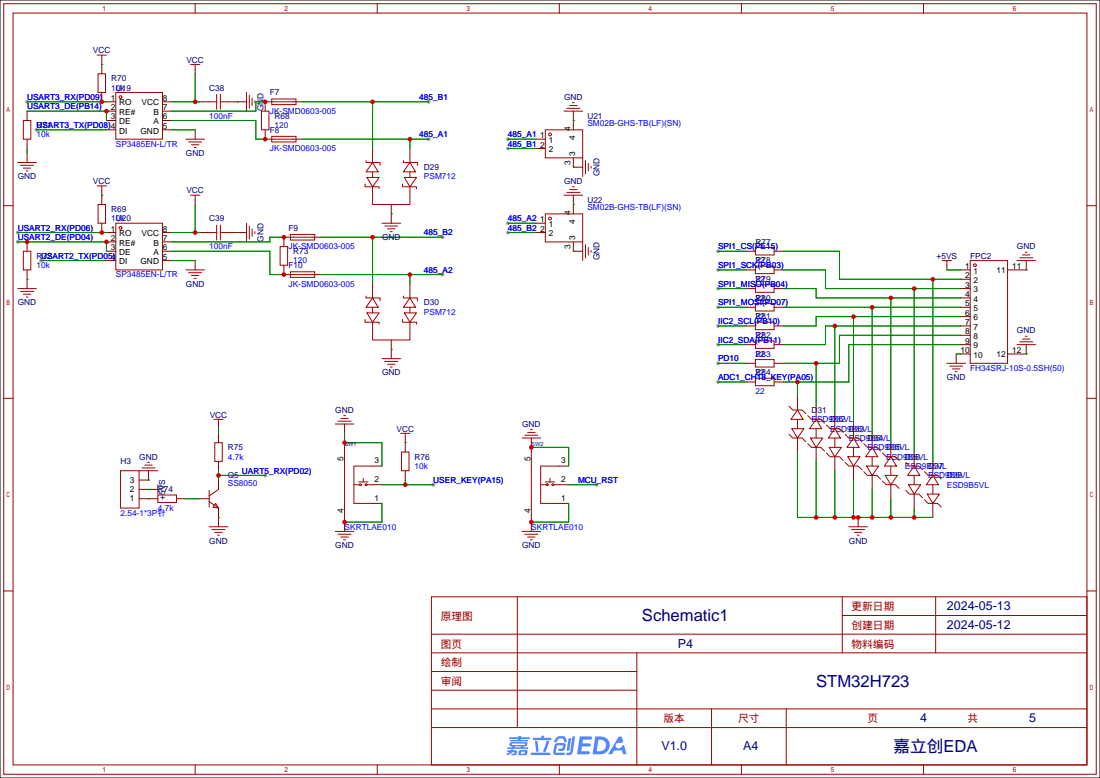
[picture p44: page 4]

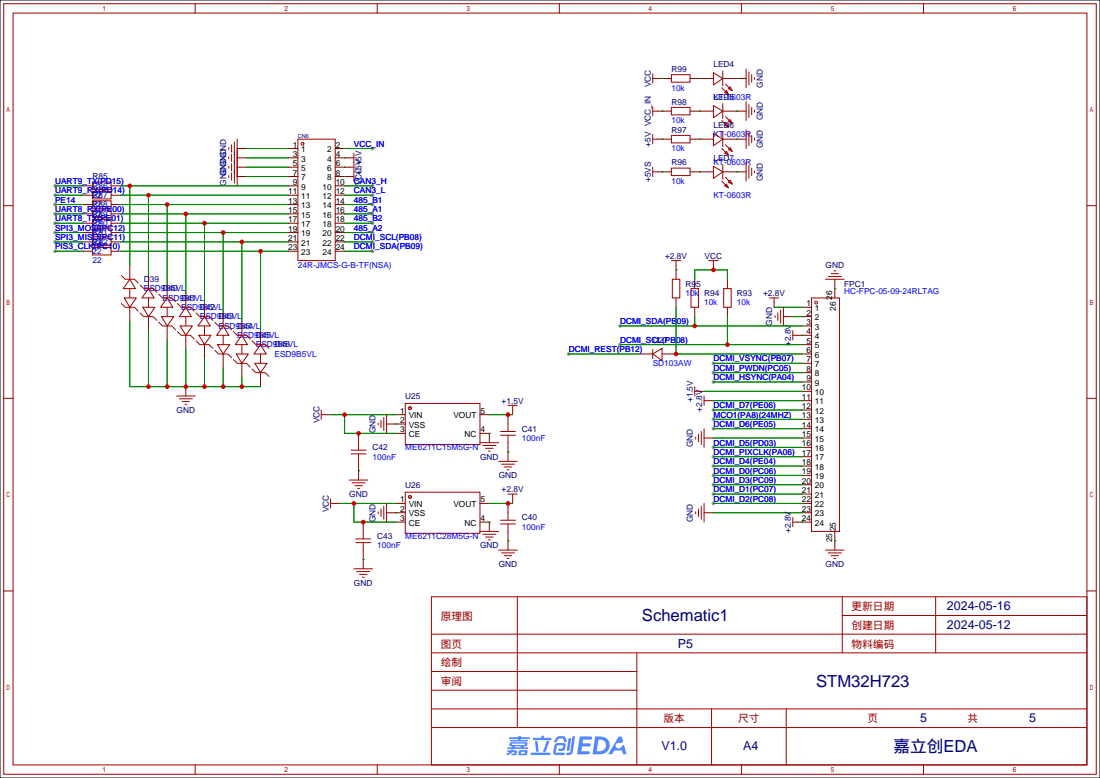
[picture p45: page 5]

GND GND

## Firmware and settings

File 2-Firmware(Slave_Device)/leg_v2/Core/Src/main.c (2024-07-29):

/* Includes ------------------------------------------------------------------*/
#include "main.h"
#include "dma.h"
#include "fdcan.h"
#include "memorymap.h"
#include "spi.h"
#include "tim.h"
#include "usart.h"
#include "gpio.h"


#include "BMI088driver.h"
#include "dm_driver.h"	


extern float pos[];//pos[0] is unused, start from pos[1]
extern float vel[];
float kp[11]={20,20,20,20,20,20,20,20,20,20,20};
float kd[11]={0.2,0.2,0.2,0.2,0.2,0.2,0.2,0.2,0.2,0.2,0.2};
float torq[11]={0,0,0,0,0,0,0,0,0,0,0};




void SystemClock_Config(void);

/* USER CODE BEGIN 0 */
float gyro[3], accel[3], temp;
/* USER CODE END 0 */

/**
  * @brief  The application entry point.
  * @retval int
  */
int main(void)
{
  /* MCU Configuration--------------------------------------------------------*/

  /* Reset of all peripherals, Initializes the Flash interface and the Systick. */
  HAL_Init();

  /* Configure the system clock */
  SystemClock_Config();

  /* Initialize all configured peripherals */
  MX_GPIO_Init();
  MX_DMA_Init();
  MX_SPI2_Init();
  MX_USART1_UART_Init();
  MX_FDCAN1_Init();
  MX_FDCAN2_Init();
  MX_TIM6_Init();
  /* USER CODE BEGIN 2 */
	can_bsp_init();	
	enable_motor_mode(&hfdcan2,1,MIT_MODE);
	HAL_Delay(100);
    enable_motor_mode(&hfdcan2,2,MIT_MODE);
	HAL_Delay(100);
	enable_motor_mode(&hfdcan2,3,MIT_MODE);
	HAL_Delay(100);
    enable_motor_mode(&hfdcan2,4,MIT_MODE);
	HAL_Delay(100);
	enable_motor_mode(&hfdcan2,5,MIT_MODE);
	HAL_Delay(100);
	enable_motor_mode(&hfdcan1,6,MIT_MODE);
	HAL_Delay(100);
    enable_motor_mode(&hfdcan1,7,MIT_MODE);
	HAL_Delay(100);
	enable_motor_mode(&hfdcan1,8,MIT_MODE);
	HAL_Delay(100);
    enable_motor_mode(&hfdcan1,9,MIT_MODE);
	HAL_Delay(100);
	enable_motor_mode(&hfdcan1,10,MIT_MODE);
	HAL_Delay(100);
    while(BMI088_init())
    {
		
    }
		HAL_TIM_Base_Start_IT(&htim6);
	while (1)
	{
    
	}
}

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


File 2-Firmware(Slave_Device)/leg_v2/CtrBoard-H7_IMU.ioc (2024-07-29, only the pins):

Mcu.UserName=STM32H723VGTx
PA10.Signal=USART1_RX
PA13(JTMS/SWDIO).Signal=DEBUG_JTMS-SWDIO
PA14(JTCK/SWCLK).Signal=DEBUG_JTCK-SWCLK
PA9.Signal=USART1_TX
PB13.Signal=SPI2_SCK
PB5.Signal=FDCAN2_RX
PB6.Signal=FDCAN2_TX
PC0.GPIO_Label=ACC_CS
PC0.Signal=GPIO_Output
PC1.Signal=SPI2_MOSI
PC2_C.Signal=SPI2_MISO
PC3_C.GPIO_Label=GYRO_CS
PC3_C.Signal=GPIO_Output
PD0.Signal=FDCAN1_RX
PD1.Signal=FDCAN1_TX
PE10.GPIO_Label=ACC_INT
PE10.Signal=GPXTI10
PE12.GPIO_Label=GYRO_INT
PE12.Signal=GPXTI12
PH0-OSC_IN.Signal=RCC_OSC_IN
PH1-OSC_OUT.Signal=RCC_OSC_OUT

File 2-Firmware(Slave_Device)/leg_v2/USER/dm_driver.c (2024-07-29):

#include "dm_driver.h"
#include "can_driver.h"
#include "fdcan.h"

/**
************************************************************************
* @brief:      	dm4310_enable: 启用DM4310电机控制模式函数
* @param[in]:   hcan:    指向CAN_HandleTypeDef结构的指针
* @param[in]:   motor:   指向motor_t结构的指针，包含电机相关信息和控制参数
* @retval:     	void
* @details:    	根据电机控制模式启用相应的模式，通过CAN总线发送启用命令
*               支持的控制模式包括位置模式、位置速度控制模式和速度控制模式
************************************************************************
**/
void dm4310_enable(FDCAN_HandleTypeDef* hcan, motor_t *motor)
{
	switch(motor->ctrl.mode)
	{
		case 0:
			enable_motor_mode(hcan, motor->id, MIT_MODE);
			break;
		case 1:
			enable_motor_mode(hcan, motor->id, POS_MODE);
			break;
		case 2:
			enable_motor_mode(hcan, motor->id, SPEED_MODE);
			break;
	}	
}
/**
************************************************************************
* @brief:      	dm4310_disable: 禁用DM4310电机控制模式函数
* @param[in]:   hcan:    指向CAN_HandleTypeDef结构的指针
* @param[in]:   motor:   指向motor_t结构的指针，包含电机相关信息和控制参数
* @retval:     	void
* @details:    	根据电机控制模式禁用相应的模式，通过CAN总线发送禁用命令
*               支持的控制模式包括位置模式、位置速度控制模式和速度控制模式
************************************************************************
**/
void dm4310_disable(FDCAN_HandleTypeDef* hcan, motor_t *motor)
{
	switch(motor->ctrl.mode)
	{
		case 0:
			disable_motor_mode(hcan, motor->id, MIT_MODE);
			break;
		case 1:
			disable_motor_mode(hcan, motor->id, POS_MODE);
			break;
		case 2:
			disable_motor_mode(hcan, motor->id, SPEED_MODE);
			break;
	}	
	dm4310_clear_para(motor);
}
/**
************************************************************************
* @brief:      	dm4310_ctrl_send: 发送DM4310电机控制命令函数
* @param[in]:   hcan:    指向CAN_HandleTypeDef结构的指针
* @param[in]:   motor:   指向motor_t结构的指针，包含电机相关信息和控制参数
* @retval:     	void
* @details:    	根据电机控制模式发送相应的命令到DM4310电机
*               支持的控制模式包括位置模式、位置速度控制模式和速度控制模式
************************************************************************
**/
void dm4310_ctrl_send(FDCAN_HandleTypeDef* hcan, motor_t *motor)
{
	switch(motor->ctrl.mode)
	{
		case 0:
			mit_ctrl(hcan, motor->id, motor->ctrl.pos_set, motor->ctrl.vel_set, motor->ctrl.kp_set, motor->ctrl.kd_set, motor->ctrl.tor_set);
			break;
		case 1:
			pos_speed_ctrl(hcan, motor->id, motor->ctrl.pos_set, motor->ctrl.vel_set);
			break;
		case 2:
			speed_ctrl(hcan, motor->id, motor->ctrl.vel_set);
			break;
	}	
}
/**
************************************************************************
* @brief:      	dm4310_set: 设置DM4310电机控制参数函数
* @param[in]:   motor:   指向motor_t结构的指针，包含电机相关信息和控制参数
* @retval:     	void
* @details:    	根据命令参数设置DM4310电机的控制参数，包括位置、速度、
*               比例增益(KP)、微分增益(KD)和扭矩
************************************************************************
**/
void dm4310_set(motor_t *motor)
{
	motor->ctrl.kd_set 	= motor->cmd.kd_set;
	motor->ctrl.kp_set	= motor->cmd.kp_set;
	motor->ctrl.pos_set	= motor->cmd.pos_set;
	motor->ctrl.vel_set	= motor->cmd.vel_set;
	motor->ctrl.tor_set	= motor->cmd.tor_set;

}
/**
************************************************************************
* @brief:      	dm4310_clear: 清除DM4310电机控制参数函数
* @param[in]:   motor:   指向motor_t结构的指针，包含电机相关信息和控制参数
* @retval:     	void
* @details:    	将DM4310电机的命令参数和控制参数清零，包括位置、速度、
*               比例增益(KP)、微分增益(KD)和扭矩
************************************************************************
**/
void dm4310_clear_para(motor_t *motor)
{
	motor->cmd.kd_set 	= 0;
	motor->cmd.kp_set	 	= 0;
	motor->cmd.pos_set 	= 0;
	motor->cmd.vel_set 	= 0;
	motor->cmd.tor_set 	= 0;
	
	motor->ctrl.kd_set 	= 0;
	motor->ctrl.kp_set	= 0;
	motor->ctrl.pos_set = 0;
	motor->ctrl.vel_set = 0;
	motor->ctrl.tor_set = 0;
}

/**
************************************************************************
* @brief:      	dm4310_clear_err: 清除DM4310电机错误函数
* @param[in]:   hcan: 	 指向CAN控制结构体的指针
* @param[in]:  	motor:   指向电机结构体的指针
* @retval:     	void
* @details:    	根据电机的控制模式，调用对应模式的清除错误函数
************************************************************************
**/
void dm4310_clear_err(FDCAN_HandleTypeDef* hcan, motor_t *motor)
{
	switch(motor->ctrl.mode)
	{
		case 0:
			clear_err(hcan, motor->id, MIT_MODE);
			break;
		case 1:
			clear_err(hcan, motor->id, POS_MODE);
			break;
		case 2:
			clear_err(hcan, motor->id, SPEED_MODE);
			break;
	}	
}

/**
************************************************************************
* @brief:      	dm4310_fbdata: 获取DM4310电机反馈数据函数
* @param[in]:   motor:    指向motor_t结构的指针，包含电机相关信息和反馈数据
* @param[in]:   rx_data:  指向包含反馈数据的数组指针
* @retval:     	void
* @details:    	从接收到的数据中提取DM4310电机的反馈信息，包括电机ID、
*               状态、位置、速度、扭矩以及相关温度参数
************************************************************************
**/
void dm4310_fbdata(motor_t *motor, uint8_t *rx_data)
{
	motor->para.id = (rx_data[0])&0x0F;
	motor->para.state = (rx_data[0])>>4;
	motor->para.p_int=(rx_data[1]<<8)|rx_data[2];
	motor->para.v_int=(rx_data[3]<<4)|(rx_data[4]>>4);
	motor->para.t_int=((rx_data[4]&0xF)<<8)|rx_data[5];
	motor->para.pos = uint_to_float(motor->para.p_int, P_MIN, P_MAX, 16); // (-12.5,12.5)
	motor->para.vel = uint_to_float(motor->para.v_int, V_MIN, V_MAX, 12); // (-45.0,45.0)
	motor->para.tor = uint_to_float(motor->para.t_int, T_MIN, T_MAX, 12);  // (-18.0,18.0)
	motor->para.Tmos = (float)(rx_data[6]);
	motor->para.Tcoil = (float)(rx_data[7]);
}
/**
************************************************************************
* @brief:      	float_to_uint: 浮点数转换为无符号整数函数
* @param[in]:   x_float:	待转换的浮点数
* @param[in]:   x_min:		范围最小值
* @param[in]:   x_max:		范围最大值
* @param[in]:   bits: 		目标无符号整数的位数
* @retval:     	无符号整数结果
* @details:    	将给定的浮点数 x 在指定范围 [x_min, x_max] 内进行线性映射，映射结果为一个指定位数的无符号整数
************************************************************************
**/
int float_to_uint(float x_float, float x_min, float x_max, int bits)
{
	/* Converts a float to an unsigned int, given range and number of bits */
	float span = x_max - x_min;
	float offset = x_min;
	return (int) ((x_float-offset)*((float)((1<<bits)-1))/span);
}

/**
************************************************************************
* @brief:      	uint_to_float: 无符号整数转换为浮点数函数
* @param[in]:   x_int: 待转换的无符号整数
* @param[in]:   x_min: 范围最小值
* @param[in]:   x_max: 范围最大值
* @param[in]:   bits:  无符号整数的位数
* @retval:     	浮点数结果
* @details:    	将给定的无符号整数 x_int 在指定范围 [x_min, x_max] 内进行线性映射，映射结果为一个浮点数
************************************************************************
**/
float uint_to_float(int x_int, float x_min, float x_max, int bits)
{
	/* converts unsigned int to float, given range and number of bits */
	float span = x_max - x_min;
	float offset = x_min;
	return ((float)x_int)*span/((float)((1<<bits)-1)) + offset;
}
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

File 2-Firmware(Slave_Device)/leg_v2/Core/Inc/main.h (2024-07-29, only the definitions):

#define ACC_CS_Pin GPIO_PIN_0
#define ACC_CS_GPIO_Port GPIOC
#define GYRO_CS_Pin GPIO_PIN_3
#define GYRO_CS_GPIO_Port GPIOC
#define ACC_INT_Pin GPIO_PIN_10
#define ACC_INT_GPIO_Port GPIOE
#define GYRO_INT_Pin GPIO_PIN_12
#define GYRO_INT_GPIO_Port GPIOE

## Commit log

2024-04-22 Add files via upload
    这是移植的达妙H723开发板的适配的驱动
2024-07-29 update the developing files
    [1 DM-J6006电机连接件.DWG, 1 DMJ6006电机连接件（加工两个）.STEP, 1 背板1.STEP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]

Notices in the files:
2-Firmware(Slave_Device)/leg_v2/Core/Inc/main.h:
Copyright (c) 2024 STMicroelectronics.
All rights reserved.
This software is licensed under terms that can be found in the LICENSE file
